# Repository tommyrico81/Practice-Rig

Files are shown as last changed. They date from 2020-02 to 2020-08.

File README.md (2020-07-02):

# R4 Street CE - Project 399 Practice Rig
The R4 Street Practice Rig takes the already bullet proof Project 399 Practice Rig Frame, and retrofits it into a DRL Style Racer 4 Canopy. This modification requires only the 2 halfplates (3mm each), and 4 arms (6mm each). There is an example of the frame build on this site showing the configuration of the carbon. If you choose to take your existing practice rig and use it in this configuration, you will require the 3D printed pieces for assembly. Please note that there are a few options depending on the setup you are using. Select the appropriate Camera Cradle for the HD DJI AirUnit or Analog Camera System. The Analog camera has been tested to fit a RunCam Racer or Microswift. The bottom shell also has two options, a 5s 1800mah battery or 5s 2200mah battery. Currently 2200mah 5s batteries are available from various online FPV stores. The 2200mah bottom canopy was designed around the Pyrodrone 2200mah 5s pack. Since the Pyrodrone Pack is slightly larger than the RDQ or CNHL Battery, these should fit as well in the battery cavity.

# Cutting Specs
* 2X Half Plates: 3mm Thick Carbon Fiber
* 4X Arms: 6mm Thick Carbon Fiber

# Hardware

* 12x M3x16mm Steel Button Head Screws (Arm screws)

* 12x M3 Steel Nyloc Nuts (Arm nuts)

* 28x M3x8mm Steel Button Head Screws (Screws for standoffs and motors)

* 8x M3x20-22mm Steel Button Head (FC Stack screws) https://pyrodrone.com/collections/hardware-and-bling/products/7075-aluminum-m3-stack-screws-choose-length

* 4X Button Head Washers (For Clamping Top Canopy) https://pyrodrone.com/collections/hardware-and-bling/products/m3-buttonhead-washer-1-pc

* 4X Anodized LockNut (For Clamping Bottom Canopy) https://pyrodrone.com/collections/hardware-and-bling/products/m3-flanged-anodized-locknut-x-1-choose-color

* 4x M3 Aluminum Nyloc Nut (FC Stack nuts)

* 4x FC Isolation Grommets (https://www.project399.com/collections/products/products/fc-isolation-grommets)

# Print Recommendations

* R4 Bottom Shell 1800mah & 2200mah & R4 Top Shell | Nylon 80-100% infill | 50mm Print Speed - Generate Support Overhang 45 degree

* R4 Cradle & R4 Rear Mount | TPU 80% infill | 30mm Print Speed - Generate Support Overhang 45 degree

Be sure to dehydrate Hydroscopic filament prior to printing!!! (Including Nylon Filament). 
$30 Food dehydrater available on Amazon for use

# Recommended Build

Build Components - https://rotorbuilds.com/build/21813

2408/2507/2510 sized motors, in 1300kv

The reason for the lower KV is to force you to learn race lines. If you're always using extra power as a crutch to fly, you wont ever learn the fast way around the track. Having a slower heavier quad forces you to keep your momentum and practice good race lines. 

5s 2200mah or 2x 1300mah packs in parallel

https://pyrodrone.com/collections/batteries/products/pyro-drone-graphene-2200mah-5s-185v-75c-by-who-cares

The larger battery helps you get as much flight time as possible. You can now full throttle for 5 minutes straight. Squeezing the most practice time out of your time at the field.

7" props

Helps get those longer flight times, also thats what we race on DRL with the R4. HQ 7x4x3 are currently the only prop that is reccomended for this build

FC and 4:1 ESC

Any reliable stack will work, The Hobbywing G3 60a ESC and FC combo is highly reccomended

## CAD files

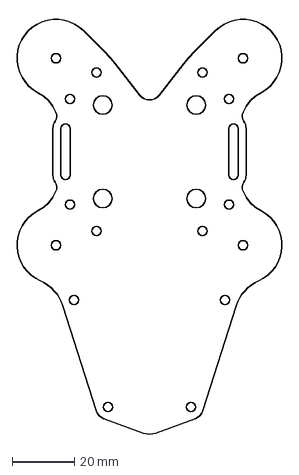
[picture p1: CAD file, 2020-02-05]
Original Practice Rig Frame Files/practice rig half plate.DXF
85.6 x 134.2 mm

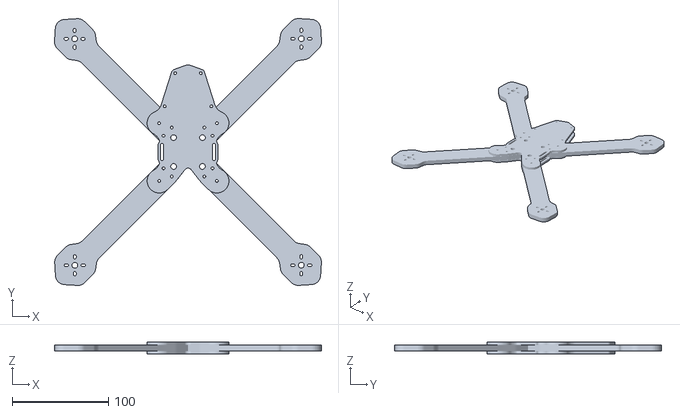
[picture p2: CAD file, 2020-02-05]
Practice Rig Frame Build Example.stl
277.4 x 277.3 x 13.0

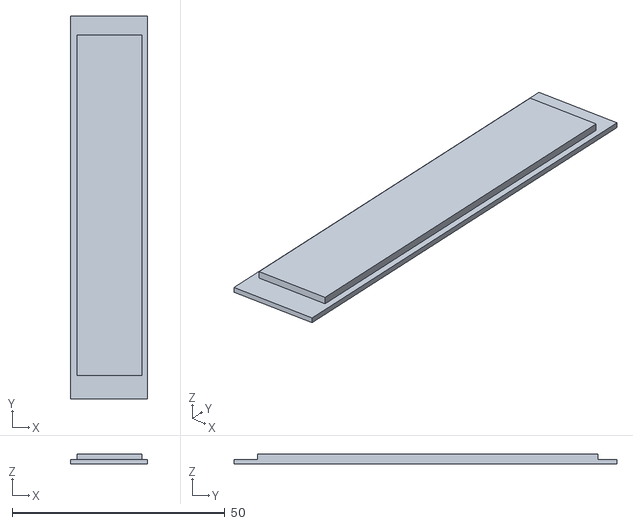
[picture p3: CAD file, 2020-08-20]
Practice Rig Frame Files/R4_TinyLED_XClass90mm.stl
18.0 x 90.0 x 2.35

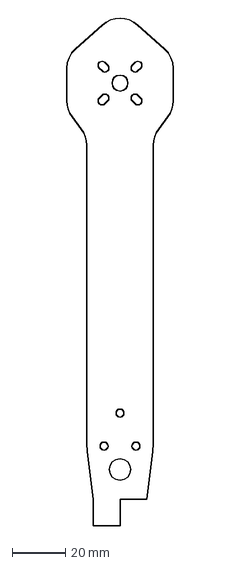
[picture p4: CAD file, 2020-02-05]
Original Practice Rig Frame Files/practice rig arm.DXF
40.0 x 191.7 mm

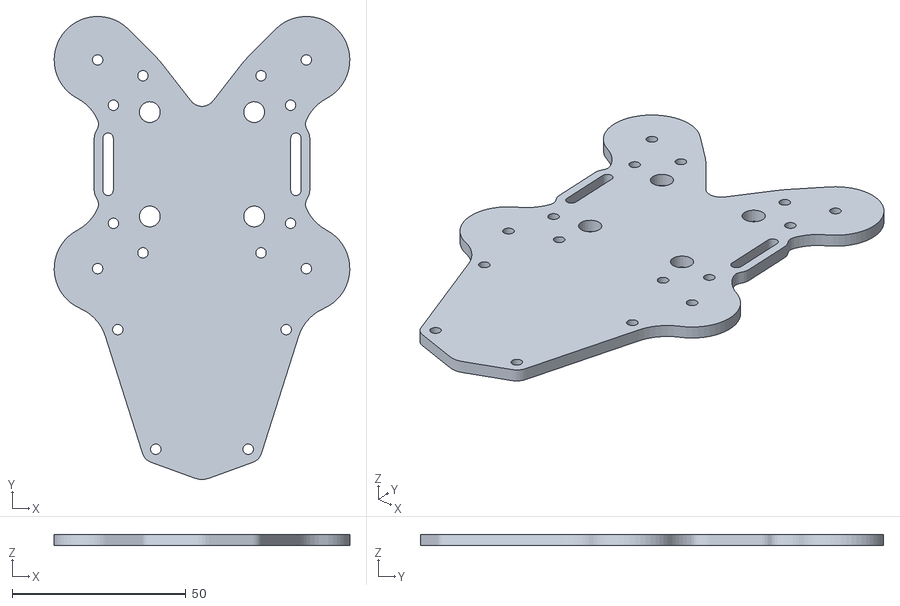
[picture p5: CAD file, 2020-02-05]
Practice Rig Frame Files/R4_Street_HalfPlate.stl
85.0 x 133.1 x 3.28

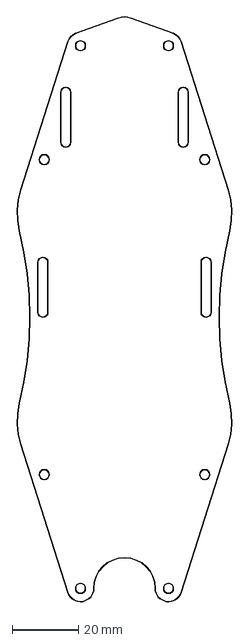
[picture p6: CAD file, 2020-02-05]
Original Practice Rig Frame Files/practice rig top plate.DXF
65.4 x 176.9 mm

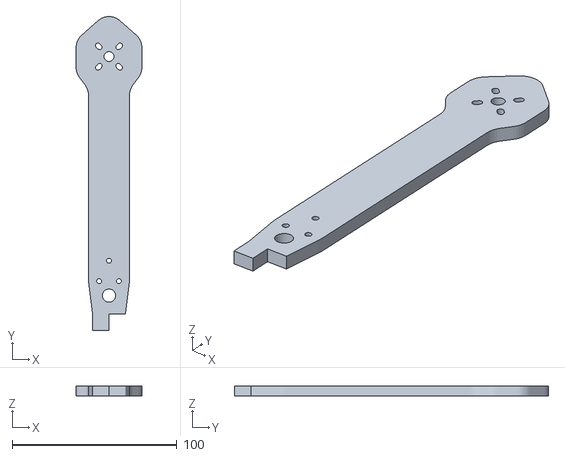
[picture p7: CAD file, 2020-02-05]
Practice Rig Frame Files/R4_Street_Arm.stl
40.0 x 190.8 x 6.20

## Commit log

2020-02-05 adding fram stls for practice rig
    [Frame R4 Shell Adapted Rig Final v1.stl, PracticeTank arm v0.stl, PracticeTank half plate v1.stl]
2020-02-05 updated frame files and organized old
    [PracticeTank arm.DXF, PracticeTank half plate.DXF, PracticeTank top plate.DXF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]
2020-02-26 added print files and updated landing page with build info
    [R4 Practice Rig Frame Build Example.stl, R4_Street_Arm.stl, R4_Street_HalfPlate.stl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]
2020-02-26 updated tail name
    [v6 R4 Tail Practice Final 22520 - Final.stl]
2020-02-26 updated landing page content, Print specs
    [v6 R4 Tail Fin Final 22520 - Final.stl]
2020-03-11 added arm guards
    [V6 R4 Arm Guards Left & Right.stl, v6 R4 Bottom Arm Guard.stl, v6 R4 Top Arm Guard.stl]
2020-03-16 DJI AirUnit Naked Mount
    [V6 DJI AirUnit Naked Mount.stl]
2020-07-02 updated project files
    [Practice Rig Frame Build Example.stl, Practice Rig Grommet.stl, R4_Street_Arm.stl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]
2020-07-02 updated file names
    [V7PrigR4Bottom2200mah.stl, V7PrigR4Topshell.stl]
2020-07-23 adding LED guards
    [V7PrigR4LEDGuard.stl, v6PrigR4RearMount.stl]
2020-08-20 added prig racewire LED guards
    [R4_TinyLED_XClass90mm.stl, V7PRigArmGuardTinyLed.stl, V7PrigR4LEDGuard.stl]
